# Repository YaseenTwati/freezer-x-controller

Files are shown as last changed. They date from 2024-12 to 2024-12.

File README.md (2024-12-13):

# Freezer X Controller

This project is a custom controller board built to replace the original controller of my freezer that stopped working. It is based on the Arduino Pro Micro and operates by reading the 10K NTC in the fridge and controlling the compressor relay.
**Note:** This controller *does not* replace the built-in compressor relay; instead, it uses an additional relay to control it.

[Dev Log Video](https://www.youtube.com/watch?v=zM9pKCJK8DQ)

**Disclaimer:** I do not recommend anyone build or use this as-is. Use it as a reference only. This was built for my specific use case, and it may or may not meet your needs.

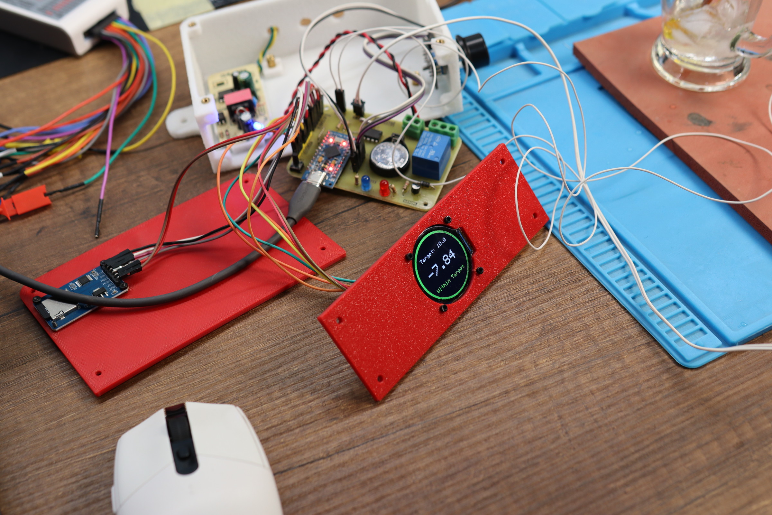
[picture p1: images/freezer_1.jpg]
Controller


<div style="display: flex; flex-direction: row; justify-content: space-around">
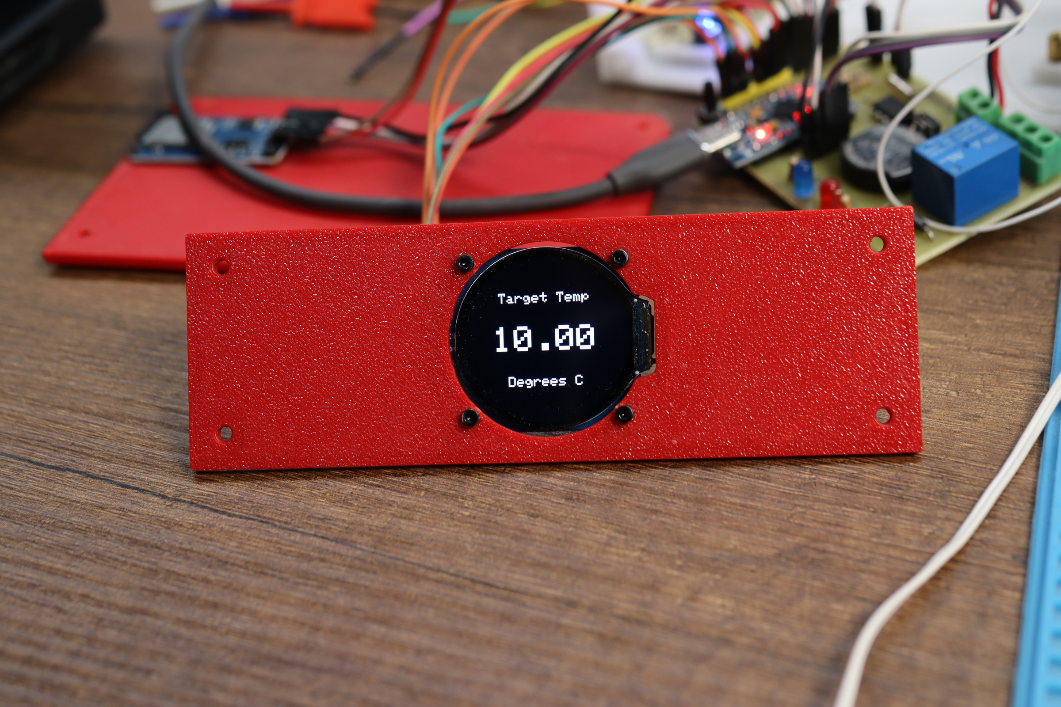
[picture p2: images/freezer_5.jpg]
    
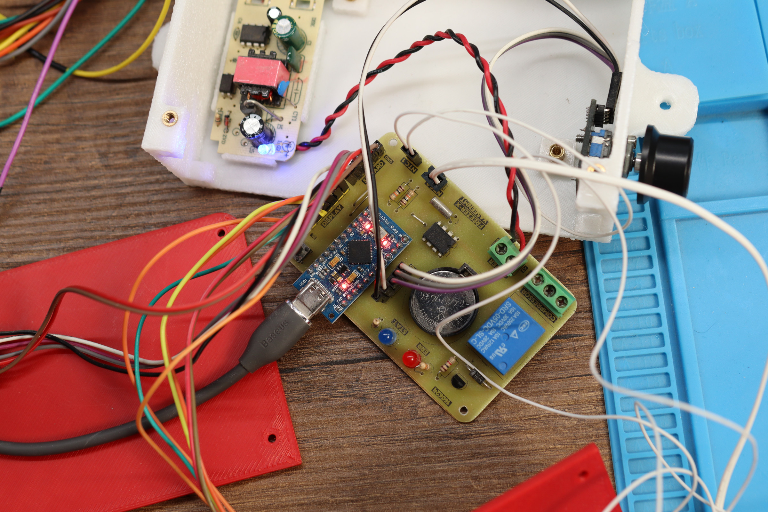
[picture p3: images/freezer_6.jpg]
    
</div>

### Features:
- Interactive menu with configurable settings (target temp, dead time, max temp, hysteresis, etc.)
- Compressor dead time (minimum time the compressor must remain off before turning on again)
- Compressor overheating protection
- NTC short/disconnection handling (min/max temp)
- Raw SD card data logging
- Startup delay

### Important Notes:
1. **RTC Clock is disabled in the code**
   The RTC clock was originally intended to add real-time data to the logs. However, the IC used proved unreliable, so the RTC functionality was disabled in the code to save space.

2. **USB Serial / CDC**
   The USB CDC peripheral is disabled in the PlatformIO configuration to save flash storage space. This means `Serial.print()` cannot be used, **and the board needs to be manually reset during code uploads.**

   You can likely re-enable it now that the RTC is disabled, as there should be enough space available.

3. **SD Card Raw Data**
   Data is logged directly to the SD card without a filesystem by sending raw SPI commands. This approach was taken as an extreme storage-saving measure since most SD card libraries require too much space.
   [I wrote a blog post about this topic if you're interested](https://yaseen.ly/writing-data-to-sdcards-without-a-filesystem-spi/).

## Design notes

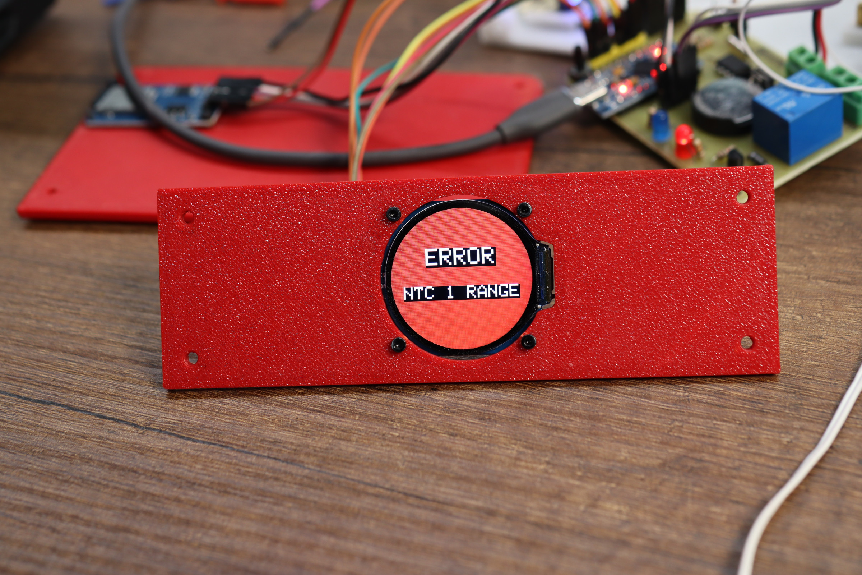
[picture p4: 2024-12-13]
images/freezer_4.jpg

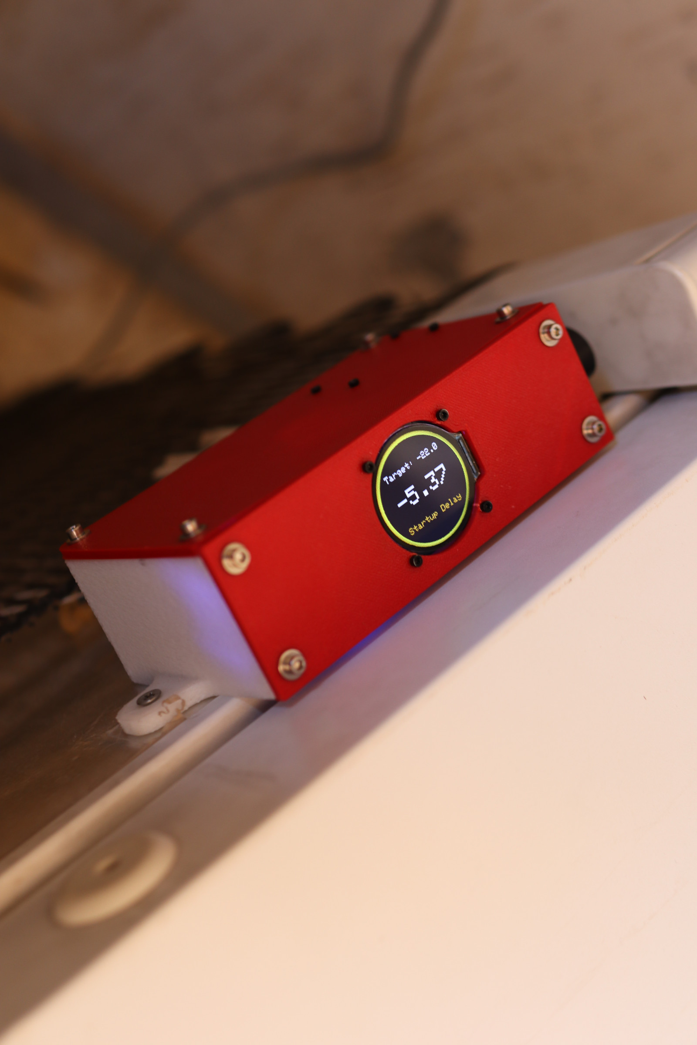
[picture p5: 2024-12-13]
images/freezer_2.jpg

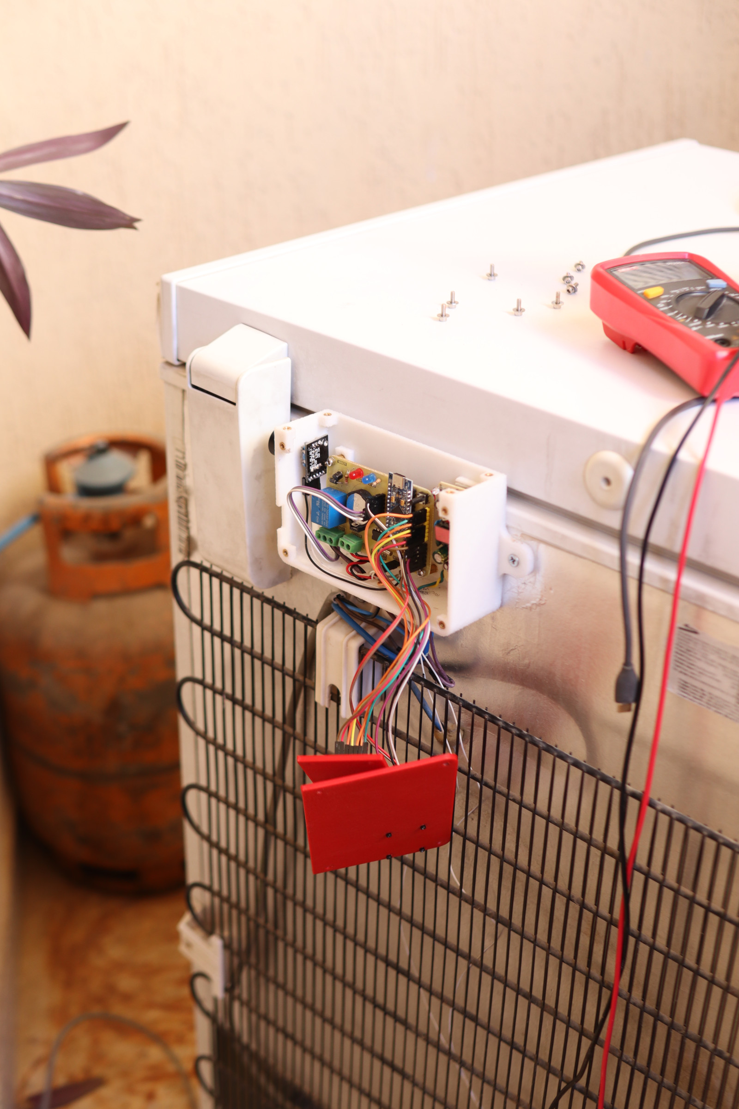
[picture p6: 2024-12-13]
images/freezer_3.jpg

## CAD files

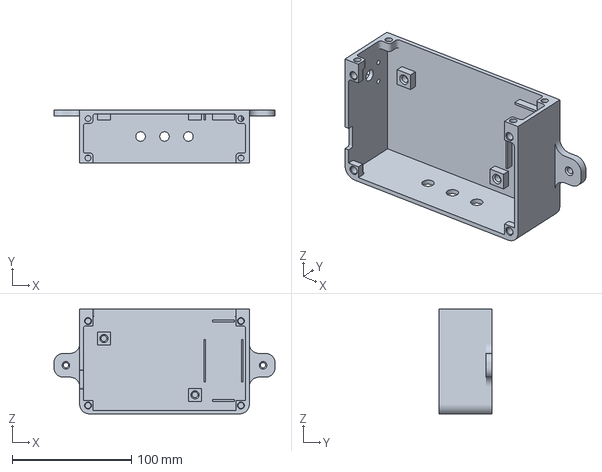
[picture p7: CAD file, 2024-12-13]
enclosure/main_body.3mf
185.0 x 44.0 x 87.7 mm

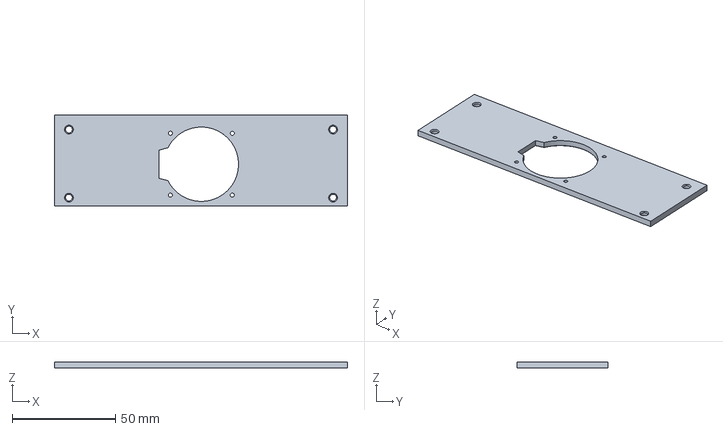
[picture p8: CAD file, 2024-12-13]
enclosure/top_cover.3mf
142.0 x 44.0 x 3.00 mm

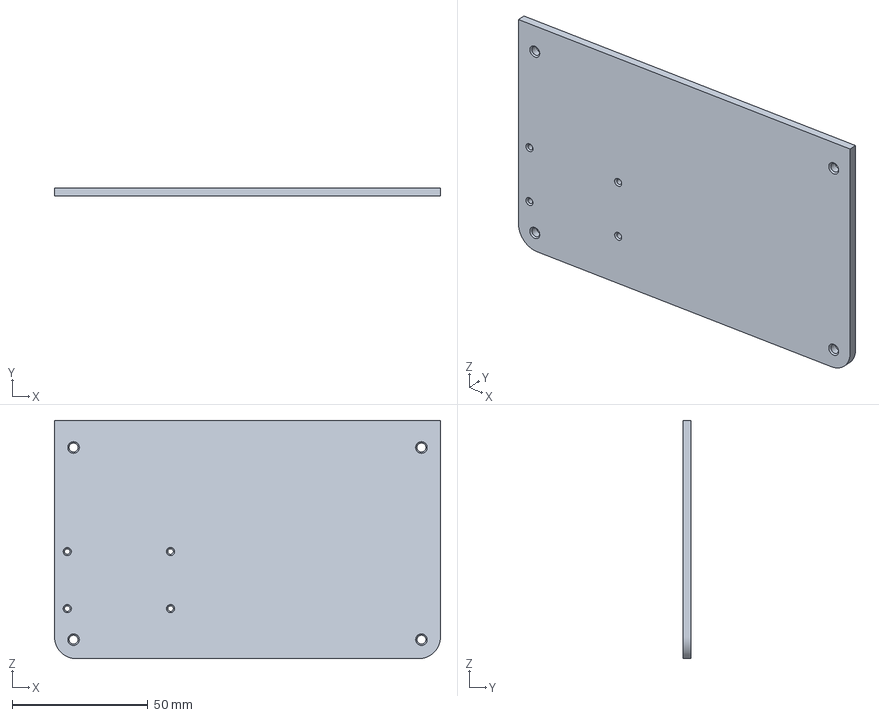
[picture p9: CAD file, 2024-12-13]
enclosure/front_cover.3mf
142.0 x 3.00 x 87.7 mm

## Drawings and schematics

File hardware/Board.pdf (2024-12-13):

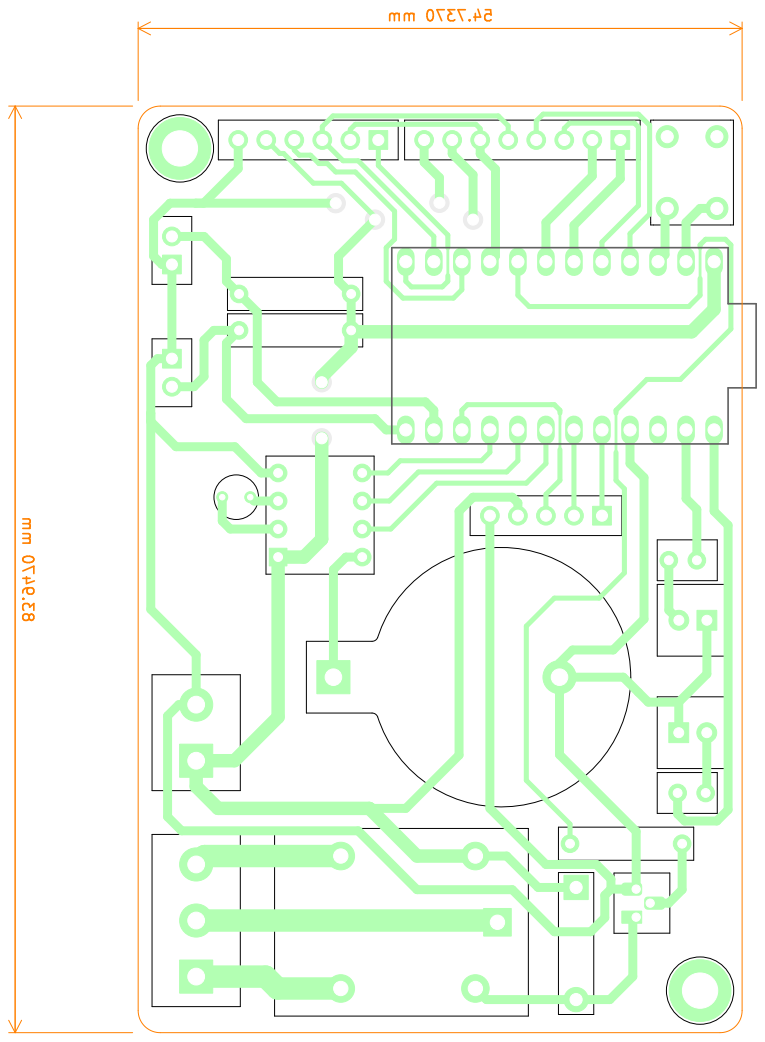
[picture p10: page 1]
D Date: KiCad; E.D.A. 8.0.6 Size: A4; Rev:; Id: 1/1 Title: Freezer X Controller File: FridgeX.kicad_pcb Sheet: Bottom; Layer -; MIRRORED; Yaseen; Twati Board2Pdf:; Bottom; MIRRORED -; Page

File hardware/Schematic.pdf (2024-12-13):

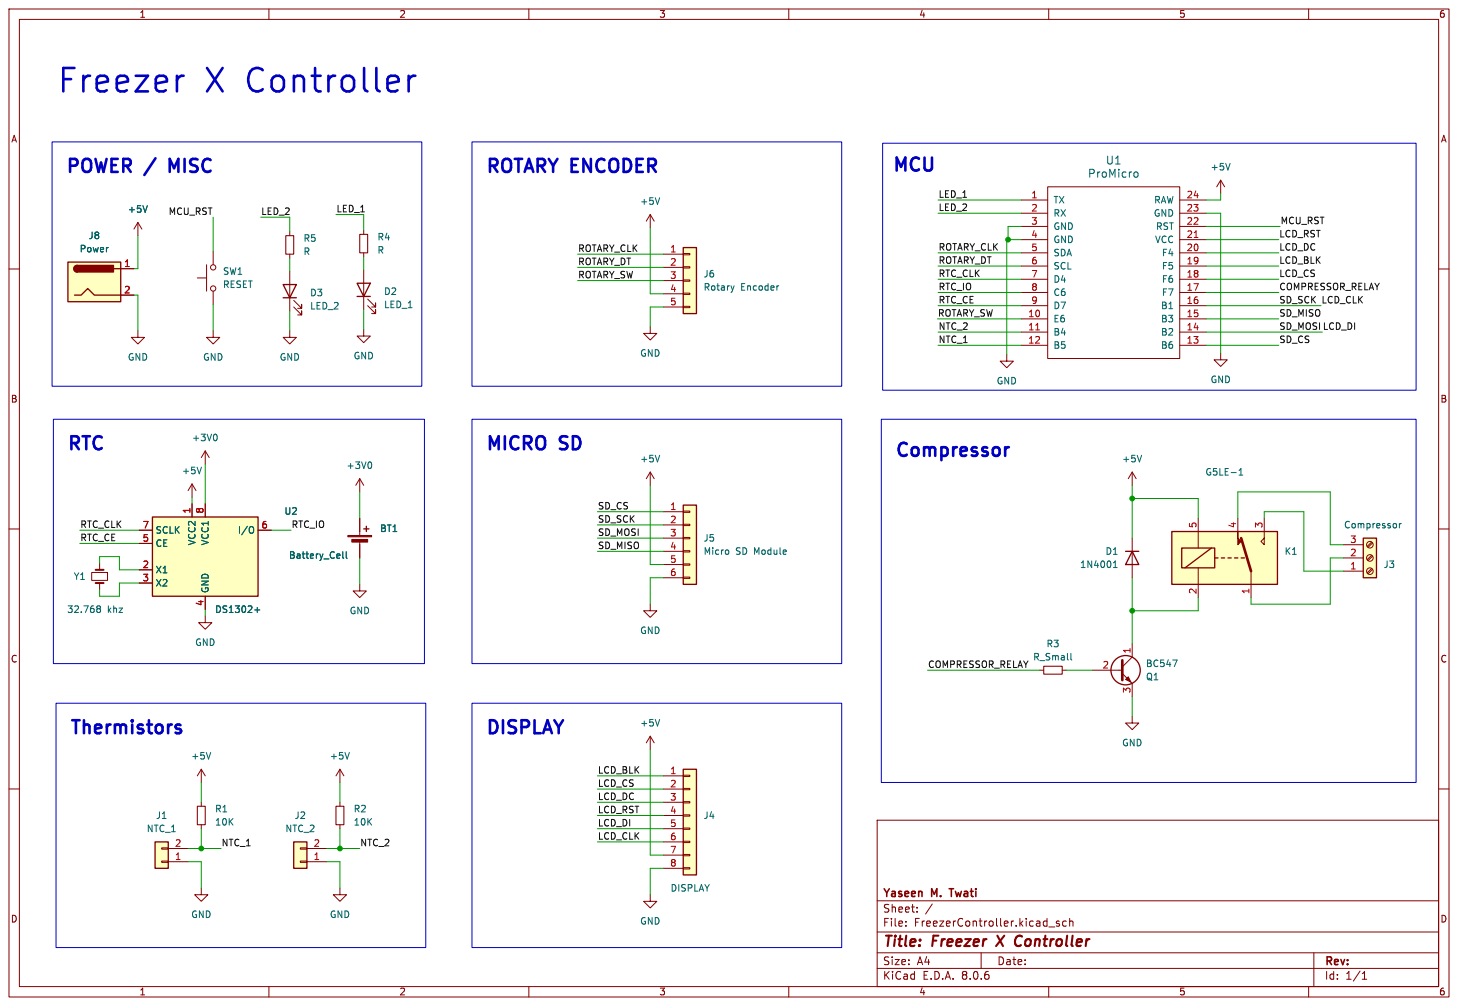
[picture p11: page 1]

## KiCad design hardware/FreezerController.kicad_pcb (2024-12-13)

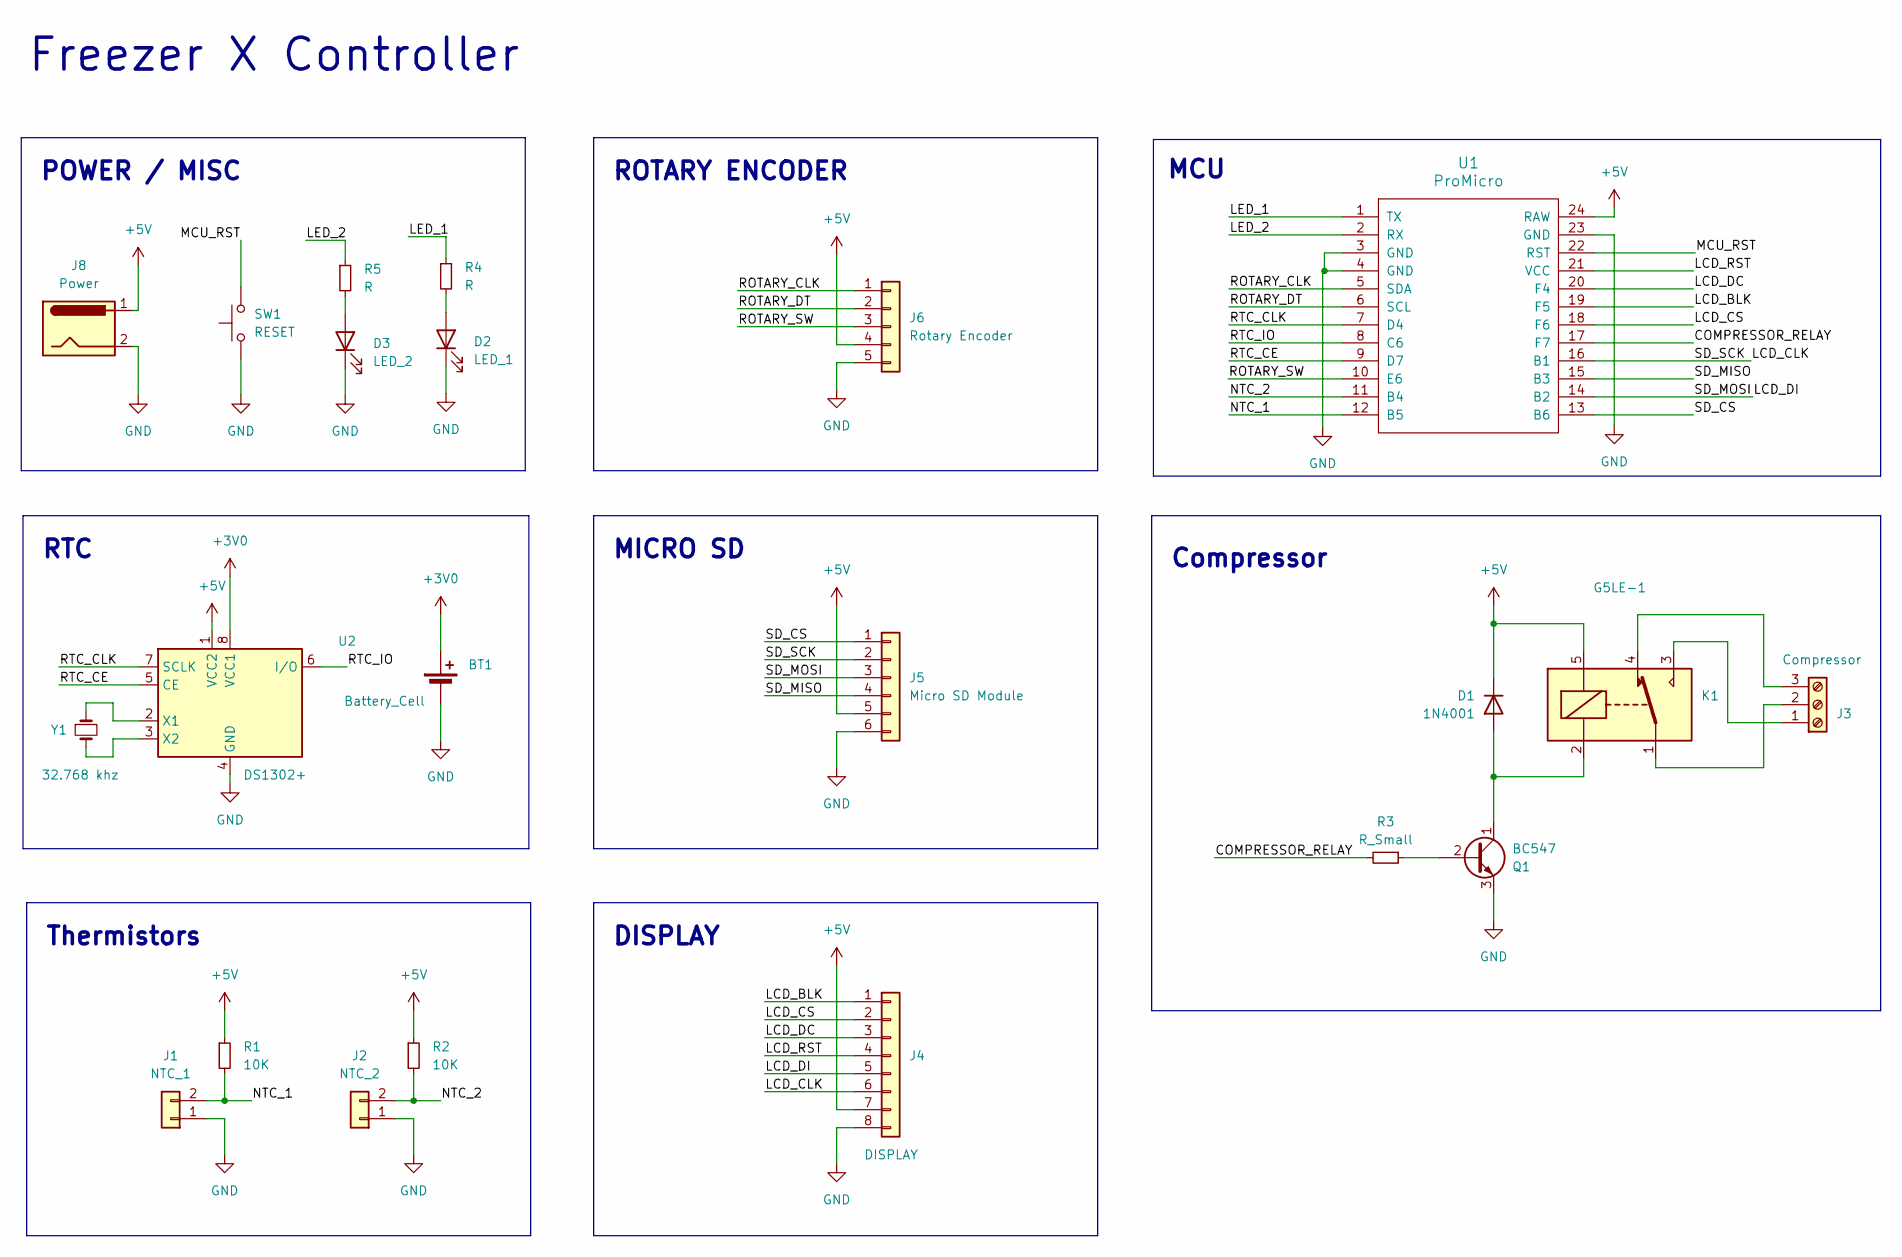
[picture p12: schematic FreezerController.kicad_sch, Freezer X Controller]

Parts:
BT1: Battery_Cell; BatteryHolder_Keystone_103_1x20mm
D1: 1N4001; D_DO-41_SOD81_P10.16mm_Horizontal
D2: LED_1; LED_D5.0mm
D3: LED_2; LED_D5.0mm
J1: NTC_1; PinHeader_1x02_P2.54mm_Vertical
J2: NTC_2; PinHeader_1x02_P2.54mm_Vertical
J3: Compressor; TerminalBlock_bornier-3_P5.08mm
J4: DISPLAY; PinHeader_1x08_P2.54mm_Vertical
J5: Micro SD Module; PinHeader_1x06_P2.54mm_Vertical
J6: Rotary Encoder; PinHeader_1x05_P2.54mm_Vertical
J8: Power; TerminalBlock_bornier-2_P5.08mm
K1: G5LE-1; Relay_SPDT_Omron-G5LE-1
Q1: BC547; TO-92L_HandSolder
R1, R2: 10K; R_Axial_DIN0207_L6.3mm_D2.5mm_P10.16mm_Horizontal
R3: R_Small; R_Axial_DIN0207_L6.3mm_D2.5mm_P10.16mm_Horizontal
R4, R5: R; R_Axial_DIN0309_L9.0mm_D3.2mm_P2.54mm_Vertical
SW1: RESET; SW_PUSH_6mm
U1: ProMicro
U2: DS1302+; DIP-8_W7.62mm
Y1: 32.768 khz; Crystal_AT310_D3.0mm_L10.0mm_Vertical

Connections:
+3V0: BT1.1 (+), U2.8 (VCC1)
+5V: D1.1 (K), J4.7, J5.5, J6.4, J8.1, K1.5, R1.1, R2.1, U1.24 (RAW), U2.1 (VCC2)
/COMPRESSOR_RELAY: R3.2, U1.17 (F7)
/LCD_BLK: J4.1, U1.19 (F5)
/LCD_CLK: J4.6, J5.2, U1.16 (B1)
/LCD_CS: J4.2, U1.18 (F6)
/LCD_DC: J4.3, U1.20 (F4)
/LCD_DI: J4.5, J5.3, U1.14 (B2)
/LCD_RST: J4.4, U1.21 (VCC)
/LED_1: R4.1, U1.1 (TX)
/LED_2: R5.1, U1.2 (RX)
/MCU_RST: SW1.2, U1.22 (RST)
/NTC_1: J1.2, R1.2, U1.12 (B5)
/NTC_2: J2.2, R2.2, U1.11 (B4)
/ROTARY_CLK: J6.1, U1.5 (SDA)
/ROTARY_DT: J6.2, U1.6 (SCL)
/ROTARY_SW: J6.3, U1.10 (E6)
/RTC_CE: U1.9 (D7), U2.5 (CE)
/RTC_CLK: U1.7 (D4), U2.7 (SCLK)
/RTC_IO: U1.8 (C6), U2.6 (I/O)
/SD_CS: J5.1, U1.13 (B6)
/SD_MISO: J5.4, U1.15 (B3)
GND: BT1.2 (-), D2.1 (K), D3.1 (K), J1.1, J2.1, J4.8, J5.6, J6.5, J8.2, Q1.3 (E), SW1.1, U1.3 (GND), U1.4 (GND), U1.23 (GND), U2.4 (GND)
unnamed: D1.2 (A), K1.2, Q1.1 (C)
unnamed: D2.2 (A), R4.2
unnamed: D3.2 (A), R5.2
unnamed: J3.1, K1.3
unnamed: J3.2, K1.1
unnamed: J3.3, K1.4
unnamed: Q1.2 (B), R3.1
unnamed: U2.2 (X1), Y1.1
unnamed: U2.3 (X2), Y1.2

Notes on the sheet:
Freezer X Controller
RTC
Compressor
ROTARY ENCODER
Thermistors
POWER / MISC
MCU
DISPLAY
MICRO SD

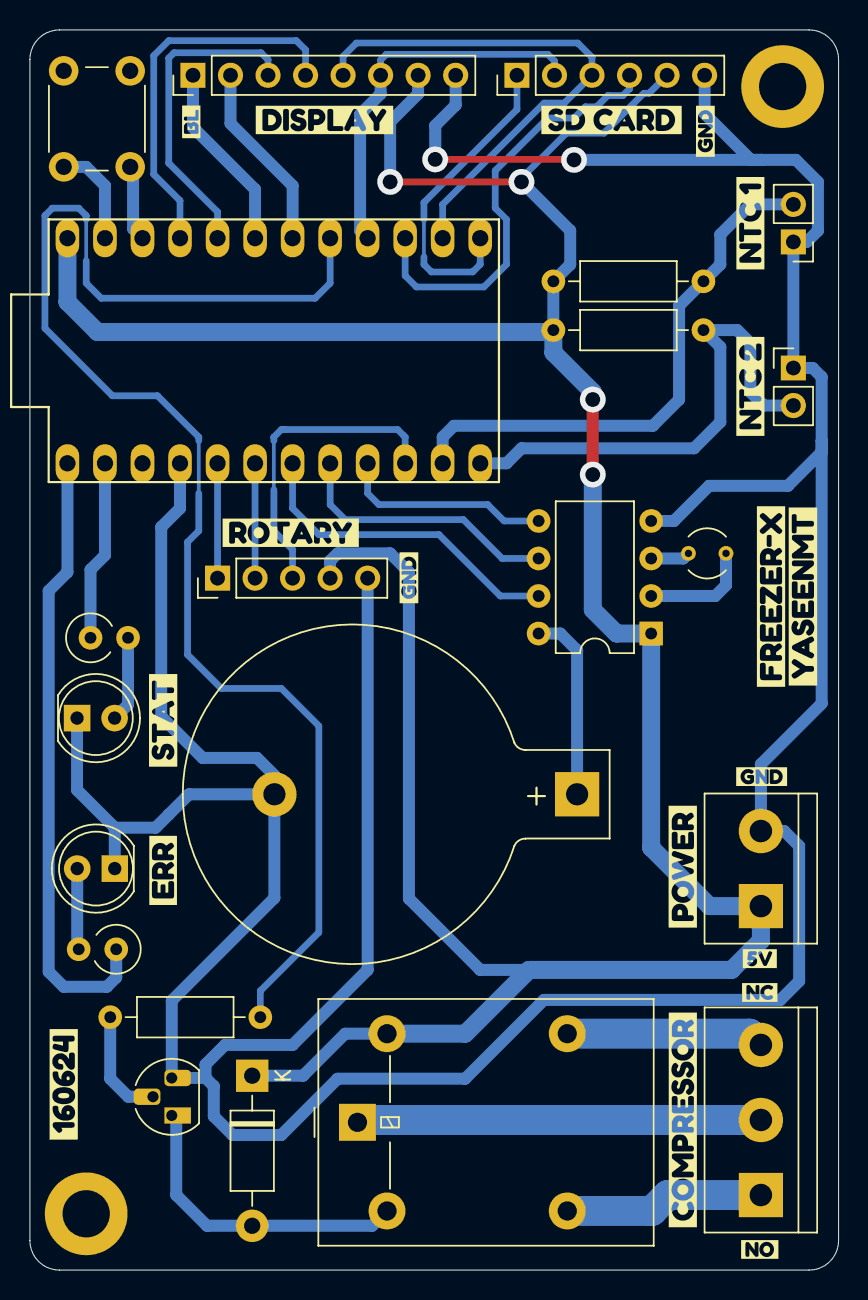
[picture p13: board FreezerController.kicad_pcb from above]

Board: 2 copper layers, 54.7 x 83.9 mm, 41 parts (0 on the bottom side), 32 nets.

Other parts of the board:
kibuzzard-666E3AD2: G***; kibuzzard-666E3AD2
kibuzzard-666E34B9: G***; kibuzzard-666E34B9
kibuzzard-666E34CF: G***; kibuzzard-666E34CF
kibuzzard-666E34E6: G***; kibuzzard-666E34E6
kibuzzard-666E35C1, kibuzzard-666E35C1#2, kibuzzard-666E35C1#3: G***; kibuzzard-666E35C1
kibuzzard-666E35CE: G***; kibuzzard-666E35CE
kibuzzard-666E35DE: G***; kibuzzard-666E35DE
kibuzzard-666E35EC: G***; kibuzzard-666E35EC
kibuzzard-666E38E3: G***; kibuzzard-666E38E3
kibuzzard-666E343D: G***; kibuzzard-666E343D
kibuzzard-666E346F: G***; kibuzzard-666E346F
kibuzzard-666E349B: G***; kibuzzard-666E349B
kibuzzard-666E394F: G***; kibuzzard-666E394F
kibuzzard-666E3446: G***; kibuzzard-666E3446
kibuzzard-666E3626: G***; kibuzzard-666E3626
kibuzzard-666E3888: G***; kibuzzard-666E3888
kibuzzard-666E3893: G***; kibuzzard-666E3893

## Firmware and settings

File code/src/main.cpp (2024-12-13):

// --------------------------------------------
// Freezer X Controller Firmware
// Yaseen M. Twati - 2024 | https://yaseen.ly
// --------------------------------------------

#include <Arduino.h>
#include <Adafruit_GC9A01A.h>
#include <EEPROM.h>
#include <Encoder.h>
#include <NTC_Thermistor.h>
#include <RtcDS1302.h>
#include <SPI.h>
#include <Thermistor.h>
#include <avr/wdt.h>

// --------------------------------------
// Pins

// Thermistors
const int THERMISTOR_1_PIN = A8;
const int THERMISTOR_2_PIN = A9;

//// RTC
const int RTC_CLK = 4;
const int RTC_IO = 5;
const int RTC_CE = 6;

// Rotary Encoder
const int ROTARY_CLK = 2;
const int ROTARY_DT = 3;
const int ROTARY_SW = 7;

// LCD
const int LCD_RST = 20;
const int LCD_DC = 21;
const int LCD_DIN = 16;
const int LCD_SCK = 15;
const int LCD_CS = 19;

// Micro SD
const int MICRO_SD_CS = 10;
const int MICRO_SD_MOSI = 16;
const int MICRO_SD_MISO = 14;
const int MICRO_SD_SCK = 15;

// Compressor Relay
const int COMPRESSOR_RELAY = 18;

// LEDs
const int BLUE_LED_PIN = 0;
const int RED_LED_PIN = 1;

// --------------------------------------
// Constants

// the int16_t don't actually have to be signed, they can be uint16_t
// but having them as signed makes it easier for me to have them wrap around in the code.

// Config Menu Constants
const float MIN_TARGET_TEMPERATURE = -22.0;
const float MAX_TARGET_TEMPERATURE = -10.0;
const float TARGET_TEMPERATURE_INCREMENT = 1.0;

const int16_t MIN_TARGET_TEMPERATURE_HYSTERESIS_TIME = 5;
const int16_t MAX_TARGET_TEMPERATURE_HYSTERESIS_TIME = 350;
const int16_t TARGET_TEMPERATURE_HYSTERESIS_TIME_INCREMENT = 10;

const int16_t MIN_COMPRESSOR_DEAD_TIME = 2;
const int16_t MAX_COMPRESSOR_DEAD_TIME = 20;
const int16_t COMPRESSOR_DEAD_TIME_INCREMENT = 1;

const int16_t MIN_COMPRESSOR_MAX_RUNTIME = 60;
const int16_t MAX_COMPRESSOR_MAX_RUNTIME = 600; // 10 hours ?
const int16_t COMPRESSOR_MAX_RUNTIME_INCREMENT = 10;

const float MIN_COMPRESSOR_MAX_TEMP = 30.0;
const float MAX_COMPRESSOR_MAX_TEMP = 60.0;
const float COMPRESSOR_MAX_TEMP_INCREMENT = 1.0;

const int16_t MIN_FREEZER_STARTUP_DELAY = 0;
const int16_t MAX_FREEZER_STARTUP_DELAY = 20;
const int16_t FREEZER_STARTUP_DELAY_INCREMENT = 1;

// NTC Constants
const int REFERENCE_RESISTANCE = 10000;
const int NOMINAL_TEMPERATURE = 25;
const int B_VALUE_NTC_1 = 3950;
const int B_VALUE_NTC_2 = 3950;

const int ANALOG_RESOLUTION = 1023;

const uint32_t NOMINAL_RESISTANCE_NTC_1 = 10000;
const uint32_t NOMINAL_RESISTANCE_NTC_2 = 100000;

// SD CARD SECTOR SIZE
const uint16_t SD_BLOCK_SIZE  = 512;

// LCD Constants
// these are mainly here to save a few bytes instead of calling tft.width() & tft.height()
const int16_t LCD_SIZE = 240; // width is same as height
const int16_t LCD_CENTER = 120;

// --------------------------------------
// Structures & Enums

struct freezer_config
{
  char magic_bytes[4] = {'F', '0', '0', '2'}; // 4

  float target_temperature = -18.0;  // Degrees Celsius // 4

  int16_t target_temperature_hysteresis_time = 60;  // 15 seconds // 2

  int16_t compressor_dead_time = 5;     // minutes // 2
  int16_t compressor_max_run_time = 300; // 5 hours // in minutes // 2

  float compressor_max_temp = 45.0; // 4

  int16_t freezer_startup_delay = 2;  // minutes; // 2
};

enum freezer_status
{
  off = 0,
  cooling = 1,
//  hysteresis = 2,
  reached_target = 2,
  dead_time = 3,
  compressor_max_runtime = 4,
  startup_delay = 5,
  overheat = 6,
};

const char* freezer_status_strings[] = {
    "",
    "   Cooling   ",
//    "",
    "Within Target",
    "  Dead Time  ",
    " Max Runtime ",
    "Startup Delay",
    "  Overheat   ",
};

uint16_t status_colors[][2] = {
    {GC9A01A_WHITE, GC9A01A_WHITE},
    {GC9A01A_BLUE, GC9A01A_PURPLE},
//    {GC9A01A_WHITE, GC9A01A_WHITE},
    {GC9A01A_GREEN, GC9A01A_GREEN},
    {GC9A01A_WHITE, GC9A01A_WHITE},
    {GC9A01A_ORANGE, GC9A01A_YELLOW},
    {GC9A01A_ORANGE, GC9A01A_YELLOW},
    {GC9A01A_RED, GC9A01A_ORANGE},
};

struct freezer_state
{
  double current_ntc1_temperature = 0.0; // 4 bytes
  double current_ntc2_temperature = 0.0; // 4 bytes

  bool target_compressor_state = LOW;
  bool actual_compressor_state = LOW;

  freezer_status status = freezer_status::off;
};

struct freezer_state_data_point
{
  volatile uint8_t start_magic_bytes[4] = {'F', 'Z', 'Z', 'X'}; // 4 bytes

//  volatile uint32_t unix_time = 0; // 8 bytes
  volatile uint32_t ms_since_startup = 0;

  freezer_config config; // 24 bytes

  freezer_state state; // 11 bytes

  volatile uint8_t crc = 0; // 4 bytes
};

struct menu_entry
{
  const char* name;
  const char* unit;

  void* value;
  bool is_float;
  float increment;
  float min;
  float max;
};

// --------------------------------------
// Peripherals

Adafruit_GC9A01A tft(LCD_CS, LCD_DC, LCD_RST);

Encoder input_rotary_encoder(ROTARY_DT, ROTARY_CLK);

Thermistor *ntc_1;
Thermistor *ntc_2;

ThreeWire rtc_three_wire(RTC_IO,RTC_CLK,RTC_CE);
RtcDS1302<ThreeWire> rtc_clock(rtc_three_wire);

// --------------------------------------
// Global Variables

bool logging_enabled = false;
bool config_is_dirty = false;
bool edit_mode = false;
bool screen_should_refresh = false;
bool showing_new_screen = false;

freezer_config active_config {};
freezer_config dirty_config {};

freezer_state current_state {};

uint32_t compressor_turned_on_at;
uint32_t compressor_turned_off_at;
uint32_t reached_target_temperature_at;
uint32_t state_updated_at = 0;
uint32_t edit_mode_toggled_at = 0;
uint32_t exceeded_max_runtime_at = 0;

int8_t screen_index;

int32_t last_encoder_position = 0;

bool startup_delay_over = false;

freezer_status previous_status = freezer_status::off;

menu_entry menu_entries[] ={
    {"Target Temp", "Degrees C", &dirty_config.target_temperature, true, TARGET_TEMPERATURE_INCREMENT, MIN_TARGET_TEMPERATURE, MAX_TARGET_TEMPERATURE},
    {"Hysteresis", "Seconds", &dirty_config.target_temperature_hysteresis_time, false, TARGET_TEMPERATURE_HYSTERESIS_TIME_INCREMENT, MIN_TARGET_TEMPERATURE_HYSTERESIS_TIME, MAX_TARGET_TEMPERATURE_HYSTERESIS_TIME},
    {"Dead Time", "Minutes", &dirty_config.compressor_dead_time, false, COMPRESSOR_DEAD_TIME_INCREMENT, MIN_COMPRESSOR_DEAD_TIME, MAX_COMPRESSOR_DEAD_TIME},
    {"Max Runtime", "Minutes", &dirty_config.compressor_max_run_time, false, COMPRESSOR_MAX_RUNTIME_INCREMENT, MIN_COMPRESSOR_MAX_RUNTIME, MAX_COMPRESSOR_MAX_RUNTIME},
    {"Max Comp Temp", "Degrees C", &dirty_config.compressor_max_temp, true, COMPRESSOR_MAX_TEMP_INCREMENT, MIN_COMPRESSOR_MAX_TEMP, MAX_COMPRESSOR_MAX_TEMP},
    {"Startup Delay", "Minutes", &dirty_config.freezer_startup_delay, false, FREEZER_STARTUP_DELAY_INCREMENT, MIN_FREEZER_STARTUP_DELAY, MAX_FREEZER_STARTUP_DELAY},
};

bool reset_by_watchdog = false;

const uint8_t HOME_SCREEN = 0;
const uint8_t INFO_SCREEN = 7;

// --------------------------------------
// Function Definitions

void initialize_thermistors();

void initialize_display();

void initialize_status_leds();

void initialize_logging();

void initialize_rtc();

void initialize_watchdog();

void initialize_compressor();

void initialize_input();

void load_config();

void save_dirty_config();

void read_sensors();

volatile void log_state();

void update_state();

void validate_temperatures();

void halt(const char* error);

bool is_compressor_overheating();

bool is_startup_delay_over();

bool is_compressor_on();

bool is_within_target_temperature();

bool has_hysteresis_time_elapsed();

bool has_compressor_exceeded_max_runtime();

bool has_dead_time_elapsed();

void set_compressor(bool state);

void handle_input();

void on_button_pressed();

void show_centered_text(const char *text, uint8_t font_size, int16_t x_offset = 0, int16_t y_offset = 0, uint16_t color = GC9A01A_WHITE);

void refresh_display();

void display_home_screen();

void display_info_screen();

bool init_sd_card();

bool save_data_point(const freezer_state_data_point* data);

bool wait_card_busy();

void send_card_command(uint8_t cmd, uint32_t arg, uint8_t crc);

uint8_t read_card_response();

bool read_card_block(uint32_t block_addr, uint8_t* buffer, uint16_t buffer_size);

bool write_card_block(uint32_t block_addr, const void* buffer, uint16_t buffer_size);

uint8_t calculate_crc8(const uint8_t *data, uint8_t len);

// --------------------------------------

void setup()
{
  initialize_watchdog();
  initialize_status_leds();

  load_config();

  initialize_logging();
  initialize_display();
  initialize_thermistors();
  initialize_compressor();
//  initialize_rtc();
  initialize_input();


  showing_new_screen = true;
  screen_should_refresh = true;
}

void loop()
{
  if(millis() - state_updated_at >= 1000) // we refresh once a second, which is more than needed
  {
    if(config_is_dirty)
    {
      active_config = dirty_config;
      config_is_dirty = false;
    }

    update_state();

    state_updated_at = millis();
  }

  handle_input();
  refresh_display();

  wdt_reset();
}

// --------------------------------------

void initialize_thermistors()
{
  // Serial.println("initialize_thermistors()");

  ntc_1 = new NTC_Thermistor(
      THERMISTOR_1_PIN,
      REFERENCE_RESISTANCE,
      NOMINAL_RESISTANCE_NTC_1,
      NOMINAL_TEMPERATURE,
      B_VALUE_NTC_1,
      ANALOG_RESOLUTION);

  ntc_2 = new NTC_Thermistor(
      THERMISTOR_2_PIN,
      REFERENCE_RESISTANCE,
      NOMINAL_RESISTANCE_NTC_2,
      NOMINAL_TEMPERATURE,
      B_VALUE_NTC_2,
      ANALOG_RESOLUTION);
}

void initialize_display()
{
  // Serial.println("initialize_display()");

  tft.begin();
  tft.setRotation(1);
  tft.fillScreen(GC9A01A_BLACK);
  tft.setTextWrap(false);
}

void initialize_status_leds()
{
  pinMode(BLUE_LED_PIN, OUTPUT);
  pinMode(RED_LED_PIN, OUTPUT);
}

void initialize_logging()
{
  // Serial.println("initialize_logging()");

  if(init_sd_card())
  {
    // Serial.println("initialize_logging(): successfully initialized sd card, enabling logging");
    logging_enabled = true;
  }
  else
  {
    // Serial.println("initialize_logging(): could not initialize sd card, logging is disabled");
  }
}

void initialize_compressor()
{
  // Serial.println("initialize_compressor()");

  pinMode(COMPRESSOR_RELAY, OUTPUT);
  digitalWrite(COMPRESSOR_RELAY, LOW);
}

void initialize_input()
{
  // Serial.println("initialize_input()");

  pinMode(ROTARY_SW, INPUT_PULLUP);
  attachInterrupt(digitalPinToInterrupt(ROTARY_SW), on_button_pressed, RISING);
}

void initialize_watchdog()
{
  reset_by_watchdog = (MCUSR & (1 << WDRF));

  MCUSR = 0;

  wdt_enable(WDTO_2S);
}

//void initialize_rtc()
//{
// // Serial.println("initialize_rtc()");
//
// rtc_clock.Begin();
//
// RtcDateTime compiled = RtcDateTime(__DATE__, __TIME__);
//
// if (!rtc_clock.IsDateTimeValid())
// {
//   // Serial.println("initialize_rtc(): RTC lost confidence in the DateTime!");
//   rtc_clock.SetDateTime(compiled);
// }
//
// if (rtc_clock.GetIsWriteProtected())
// {
//     // Serial.println("initialize_rtc(): RTC was write protected, enabling writing now");
//     rtc_clock.SetIsWriteProtected(false);
// }
//
// if (!rtc_clock.GetIsRunning())
// {
//     // Serial.println("initialize_rtc(): RTC was not actively running, starting now");
//     rtc_clock.SetIsRunning(true);
// }
//
// RtcDateTime now = rtc_clock.GetDateTime();
// if (now < compiled)
// {
//     // Serial.println("initialize_rtc(): RTC is older than compile time!  (Updating DateTime)");
//     rtc_clock.SetDateTime(compiled);
// }
//}

// --------------------------------------

void load_config()
{
  // Serial.println("load_config()");

  freezer_config config;
  EEPROM.get(0, config);

  // make sure we have a valid config by comparing the magic bytes, otherwise reset to the default state
  if(memcmp(config.magic_bytes, "F002", 4) != 0)
  {
    // we flash the LEDs just to indicate that we are resetting the config

    digitalWrite(BLUE_LED_PIN, HIGH);
    digitalWrite(RED_LED_PIN, HIGH);

    delay(1000);

    digitalWrite(BLUE_LED_PIN, LOW);
    digitalWrite(RED_LED_PIN, LOW);

    // Serial.println("load_config(): config in eeprom is invalid, resetting back to default values");

    active_config = freezer_config();
    dirty_config = freezer_config();

    save_dirty_config();
  }
  else
  {
    // Serial.println("load_config(): successfully loaded config from eeprom");

    active_config = config;
    dirty_config = config;
  }
}

void save_dirty_config()
{
  // Serial.println("save_dirty_config()");

  EEPROM.put(0, dirty_config);
}

// --------------------------------------

bool is_compressor_overheating()
{
  return current_state.current_ntc2_temperature >= active_config.compressor_max_temp;
}

bool is_startup_delay_over()
{
  return millis() >= ((uint32_t)active_config.freezer_startup_delay * 60 * 1000);
}

bool is_compressor_on()
{
  return current_state.actual_compressor_state;
}

bool is_within_target_temperature()
{
  // todo: add a 'range'
  return current_state.current_ntc1_temperature <= active_config.target_temperature;
}

bool has_hysteresis_time_elapsed()
{
  return millis() - reached_target_temperature_at >= ((uint32_t)active_config.target_temperature_hysteresis_time * 1000);
}

bool has_compressor_exceeded_max_runtime()
{
  if(exceeded_max_runtime_at > 0)
  {
    // we already exceeded the max runtime, we need to make sure we have stopped for enough time
    if(has_dead_time_elapsed())
    {
      exceeded_max_runtime_at = 0;
      return false;
    }

    return true;
  }
  else
  {
    if(is_compressor_on())
    {
      if(millis() - compressor_turned_on_at >= ((uint32_t)active_config.compressor_max_run_time * 1000 * 60))  // 28612 bytes ( THIS IS SMALLER )
      {
        exceeded_max_runtime_at = millis();
        return true;
      }
    }
  }

  exceeded_max_runtime_at = 0;
  return false;
}

bool has_dead_time_elapsed()
{
  if(compressor_turned_off_at == 0)
  {
    return true;
  }

  return millis() - compressor_turned_off_at >= ((uint32_t)active_config.compressor_dead_time * 1000 * 60);
}

void update_state()
{
  read_sensors();
  validate_temperatures();

  // we are saving startup_delay_over into a variable to make we dont get affected by millis() rolling over after 50 days or so
  if(!startup_delay_over)
  {
    startup_delay_over = is_startup_delay_over();

    if(screen_index == HOME_SCREEN || screen_index == INFO_SCREEN)
    {
      screen_should_refresh = true;
    }

    current_state.status = freezer_status::startup_delay;
    log_state();

    return;
  }

  // base decision-making -----

  if(is_within_target_temperature())
  {
    if(reached_target_temperature_at == 0)
    {
      reached_target_temperature_at = millis();
    }

    if(has_hysteresis_time_elapsed())
    {
      current_state.target_compressor_state = LOW;
      current_state.status = freezer_status::reached_target;
    }
    else
    {
      current_state.target_compressor_state = HIGH;
      current_state.status = freezer_status::cooling;
    }
  }
  else
  {
    reached_target_temperature_at = 0;

    current_state.target_compressor_state = HIGH;
    current_state.status = freezer_status::cooling;
  }

  // overrides -------

  bool override = false;

  // we only need to override if we are planning on turning on the compressor
  if(current_state.target_compressor_state == HIGH)
  {
    if(is_compressor_overheating())
    {
      current_state.status = freezer_status::overheat;
      override = true;
    }
    else if(has_compressor_exceeded_max_runtime())
    {
      current_state.status = freezer_status::compressor_max_runtime;
      override = true;
    }
    else if(!is_compressor_on() && !has_dead_time_elapsed())
    {
      current_state.status = freezer_status::dead_time;
      override = true;
    }
  }

  set_compressor(current_state.target_compressor_state && !override);
  log_state();

  screen_should_refresh = true;
}

void read_sensors()
{
//  delay(10);

  analogRead(THERMISTOR_1_PIN); // dummy read to stabilize the value

  double ntc_1_avg = 0;
  for(int i = 0; i < 10; i++)
  {
    ntc_1_avg += ntc_1->readCelsius();
  }

  current_state.current_ntc1_temperature = ntc_1_avg / 10;

//  delay(10);

  analogRead(THERMISTOR_2_PIN); // dummy read to stabilize the value

  double ntc_2_avg = 0;
  for(int i = 0; i < 10; i++)
  {
    ntc_2_avg += ntc_2->readCelsius();
  }

  current_state.current_ntc2_temperature = ntc_2_avg / 10;
}

void halt(const char* error)
{
  set_compressor(false);

  digitalWrite(RED_LED_PIN, HIGH);

  tft.fillScreen(GC9A01A_RED);

  show_centered_text("ERROR", 4, 0, -30);
  show_centered_text(error, 3, 0, 20);

  for(;;);
}

void validate_temperatures()
{
  if(current_state.current_ntc1_temperature < -100 || current_state.current_ntc1_temperature > 100)
  {
    halt("N1");
  }

  // for the compressor ntc, we don't really care if its disconnected since it'll return -273.15
  // we do care if its shorted though which would return MAX_TEMP
  if(current_state.current_ntc2_temperature > 100)
  {
    halt("N2");
  }
}

// --------------------------------------

void set_compressor(bool state)
{
  if(state != current_state.actual_compressor_state)
  {
    // if we off and going on
    if(state == HIGH)
    {
      compressor_turned_on_at = millis();
      compressor_turned_off_at = 0;
    }
    else
    {
      compressor_turned_off_at = millis();
      compressor_turned_on_at = 0;
    }

    digitalWrite(COMPRESSOR_RELAY, state);
    digitalWrite(BLUE_LED_PIN, state);

    current_state.actual_compressor_state = state;
  }
}

// --------------------------------------

void show_centered_text(const char *text, uint8_t font_size, int16_t x_offset, int16_t y_offset, uint16_t color)
{
  tft.setTextSize(font_size);
  tft.setTextColor(color, GC9A01A_BLACK);

  // Get text dimensions
  int16_t x1, y1;
  uint16_t text_width, text_height;
  tft.getTextBounds(text, 0, 0, &x1, &y1, &text_width, &text_height);

  // start with the center of the screen
  int16_t cursor_x = LCD_CENTER;
  int16_t cursor_y = LCD_CENTER;

  // shift by the offset, so a +100 means on the positive edge
  cursor_x += cursor_x * ((float)x_offset / 100);
  cursor_y += cursor_y * ((float)y_offset / 100);

  // shift back by half of the text size
  cursor_x -= text_width / 2;
  cursor_y -= text_height / 2;

  tft.setCursor(cursor_x, cursor_y);
  tft.print(text);
}

void draw_outer_ring(int16_t start_color, int16_t end_color)
{
  int16_t start_r = (start_color >> 11) & 0x1F;
  int16_t start_g = (start_color >> 5) & 0x3F;
  int16_t start_b = start_color & 0x1F;

  int16_t end_r = (end_color >> 11) & 0x1F;
  int16_t end_g = (end_color >> 5) & 0x3F;
  int16_t end_b = end_color & 0x1F;

  for (int i = 0; i < 8; i++)
  {
    float progress = (float)i / 7;

    int16_t r = start_r + (end_r - start_r) * progress;
    int16_t g = start_g + (end_g - start_g) * progress;
    int16_t b = start_b + (end_b - start_b) * progress;

    // Convert RGB to 16-bit color
    uint16_t color = (r << 11) | (g << 5) | b;

    int current_radius = LCD_CENTER - i;

    tft.drawCircle(LCD_CENTER, LCD_CENTER, current_radius, color);
  }
}

void display_home_screen()
{
  if(showing_new_screen || current_state.status != previous_status)
  {
    previous_status = current_state.status;
    showing_new_screen = false;
    draw_outer_ring(status_colors[current_state.status][0], status_colors[current_state.status][1]);
  }

  if(screen_should_refresh)
  {
    char target_str[16];
    dtostrf(active_config.target_temperature, 4, 1, target_str);

    char target_text[32];
    sprintf(target_text, "Target: %s", target_str);

    show_centered_text(target_text, 2, 0, -50);

    char current_temp_str[16];
    dtostrf(current_state.current_ntc1_temperature, 5, 2, current_temp_str);

    show_centered_text(current_temp_str, 5, 0, 0);
    show_centered_text(freezer_status_strings[current_state.status], 2, 0, 50, status_colors[current_state.status][0]);

    screen_should_refresh = false;
  }
}

void display_info_screen()
{
  if(showing_new_screen)
  {
    showing_new_screen = false;
  }

  if(screen_should_refresh)
  {
    char display_str[16];
    char ntc_str[16];

    dtostrf(current_state.current_ntc1_temperature, 4, 1, ntc_str);
    sprintf(display_str, "NTC1: %s", ntc_str);
    show_centered_text(display_str, 2, 0, -55);

    dtostrf(current_state.current_ntc2_temperature, 4, 1, ntc_str);
    sprintf(display_str, "NTC2: %s", ntc_str);
    show_centered_text(display_str, 2, 0, -30);

//    RtcDateTime now = rtc_clock.GetDateTime();
//
//    char date_str[16];
//    sprintf(date_str, "%04d-%02d-%02d", now.Year(), now.Month(), now.Day());
//
//    char time_str[16];
//    sprintf(time_str, "%02d:%02d:%02d", now.Hour(), now.Minute(), now.Second());
//
//    show_centered_text(date_str, 2, 0, 0);
//    show_centered_text(time_str, 2, 0, 20);
//

    char millis_str[16];
    sprintf(millis_str, "MS: %lu", millis());

    show_centered_text(reset_by_watchdog ? "W RESET: YES" : "W-RESET: NO", 2, 0, 0, reset_by_watchdog ? GC9A01A_RED : GC9A01A_GREEN);

    show_centered_text(millis_str, 2, 0, 20);

    show_centered_text(logging_enabled ? "LOG (TRUE)" : "LOG (FALSE)", 2, 0, 50, logging_enabled ? GC9A01A_GREEN : GC9A01A_RED);

    screen_should_refresh = false;
  }
}

void display_config_screen(int32_t config_index)
{
  if(showing_new_screen)
  {
    showing_new_screen = false;
  }

  if(screen_should_refresh)
  {
    // clear
    menu_entry entry = menu_entries[config_index];

    show_centered_text(entry.name, 2, 0, -50);
    show_centered_text(entry.unit, 2, 0, 50);

    char value_str[32];

    if (entry.is_float)
    {
      dtostrf(*(float*)entry.value, 5, 2, value_str);
    } else {
      itoa(*(uint32_t*)entry.value, value_str, 10);
    }

    tft.fillRect(0, 80, 400, 70, GC9A01A_BLACK);

    show_centered_text(value_str, 5, 0, 0, edit_mode ? GC9A01A_YELLOW : GC9A01A_WHITE);

    screen_should_refresh = false;
  }
}
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
